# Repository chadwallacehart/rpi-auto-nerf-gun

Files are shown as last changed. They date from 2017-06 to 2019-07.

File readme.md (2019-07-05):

# Automatic Nerf Gun using a Rapsberry Pi

Make a software controlled Nerf Gun using a Raspberry Pi, a servo, and some 3D printed parts.

What you'll need:
* Nerf Revelle Rapid Red Blaster - <$12 on [Amazon](https://www.amazon.com/Nerf-Rebelle-Rapid-Red-Blaster/dp/B00INZO30M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)
* Raspberry Pi with one of the PCM GPIO pins available
* A 9g servo - like [these](https://www.amazon.com/s/ref=nb_sb_noss_1?url=search-alias%3Dtoys-and-games&field-keywords=9g+servo)
* Relay switch for the Raspberry Pi - I have an odd setup from an existing project so I don't discuss this
* Access to a 3D Printer - you can use an online service
* Some 18 to 22 guage wire
* Some aligator clips, appropriate jumper pins or a breakout board for the Pi

## Software

### Installation

```
git clone https://github.com/chadwallacehart/rpi-auto-nerf-gun.git
cd rpi-auto-nerf-gun
npm install
```

### Servo.js

Set the servo to a minimum value: `sudo node servo -40` - where the enumber is the minimum value

Set the servo to a min value and then max: `sudo node servo -40 270` - first parameter is min, second is max

Sweep the servo between whatever min and max value is in the code: `sudo node servo`

### gun.js

Shoot one bullet: `sudo node gun`

Shoot any number of darts: `sudo node gun 12` - fires 12 darts

## Hardware setup

### Servo Wiring
See Adafruit's [guide](https://learn.adafruit.com/adafruits-raspberry-pi-lesson-8-using-a-servo-motor/hardware) for how to set this up.

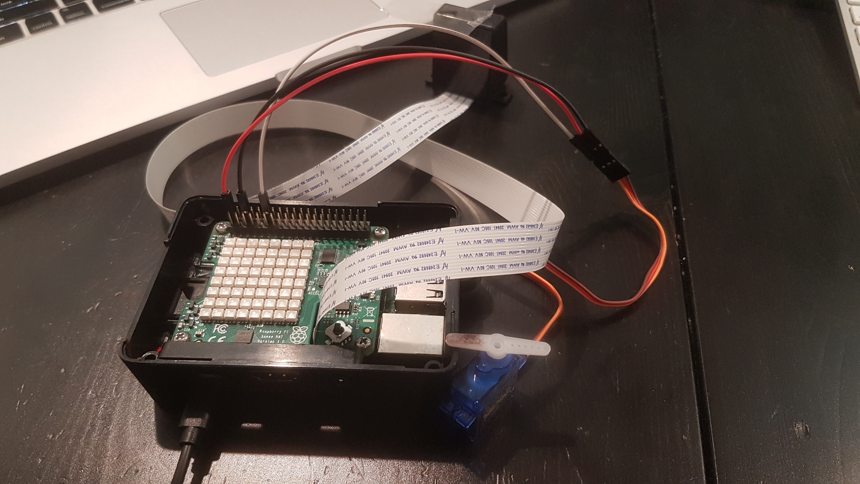
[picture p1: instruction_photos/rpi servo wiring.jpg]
Servo Setup Servo wiring


Use _servo.js_ to test.

_Note on powering_

Adafruit shows an external power supply, separate from the Raspberry Pi's. 
You shoud do this! I was able to do some tests powering directly from the Pi's 5V supply, but it was inconsistent and I wasn't being too safe. 
You can power the servo from your gun. Once you have your gun open (see below), use some aligator clips to power off of the nerf gun's batteries as shown here:

Nerf Gun wiring - servo power Powering the servo from the nerf gun

### Linear Actuator

See this [video](https://www.youtube.com/watch?v=qBHvMHJEG-M&t=1s) from Roger Rabbit of this in action.

You will need to 3d print this component and fit it inside the gun.

#### 3D printing parts

Grab the linear actuator 3D model in the repo [here](https://github.com/chadwallacehart/rpi-auto-nerf-gun/blob/master/CAD/servo%20linear%20actuator%20adjustment%203.stl).

I made a slight modification to [tscha70's](https://github.com/tscha70) [original design](https://github.com/tscha70/3DPrinterSTLFiles/tree/master/Proton%20Rev%202%20-%20Easter%20Edition) to change the size of the piston head square. 

The piston head is actually to square, so I ended up filing it down with a Dremel to look more like the angled profile of the original piston head. When I work on this again I will update the design so that this is not necessary.

#### Adjustment

You want to adjust the servo gear position so that it provides the maximum extension. 
To do this, take apart the linear relay piece so you just see the gear.

First find the minimum range. Run `sudo node servo n` with a range of values starting with 0.  
Keep decreasing _n_ until the decreasing the value makes no difference. For me this was `-40`. Mark this point.

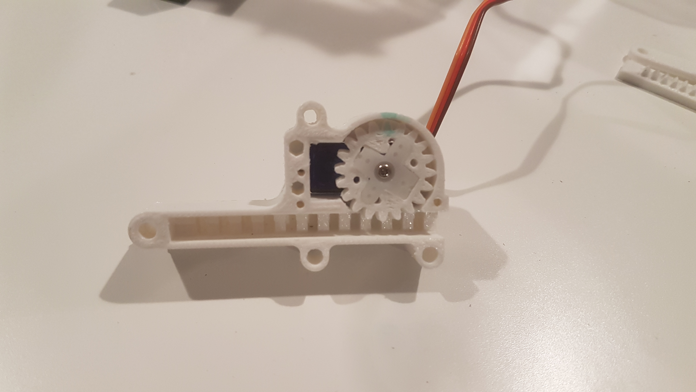
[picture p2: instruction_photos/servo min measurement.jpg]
Servo adjustment - minimum Find the servo minimium


Repeat this step to find the maximum range. Mine was `280`.

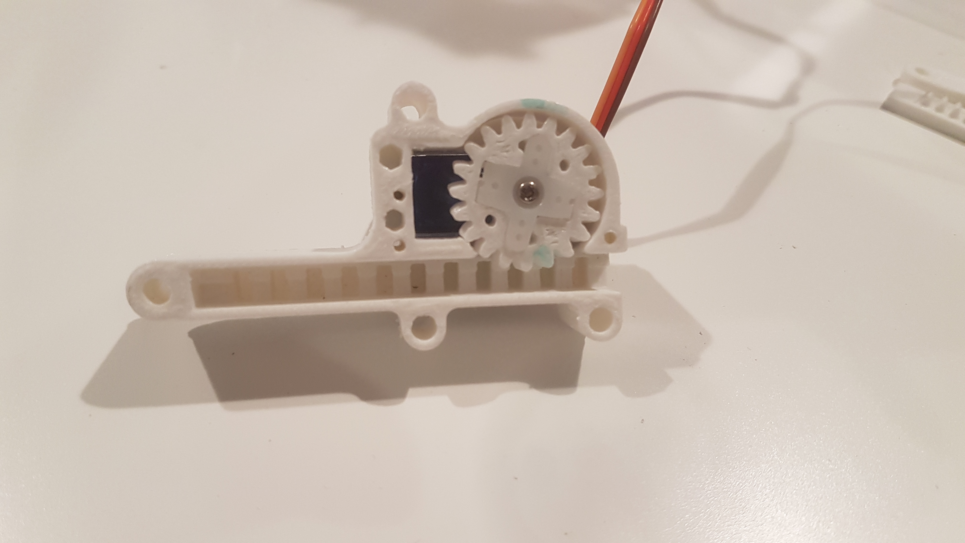
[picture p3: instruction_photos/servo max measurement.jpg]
Servo adjustment - maximum Find the servo maximum


After you find the maximum, make sure to reset the servo to its minimum point before re-assembling the linear servo.
When you are done you should have about a 38mm / 1.5 inch range.

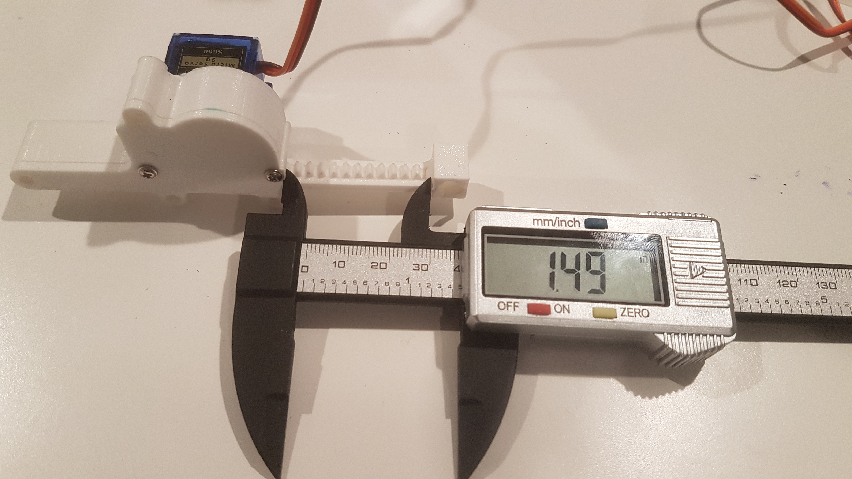
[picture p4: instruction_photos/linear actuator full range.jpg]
Adjusting to achieve the maximum linear servo range Test the servo to make sure you have the full range


Make sure to test the full range of motion many times before proceeding. 
Wiggle the actuator and simulate what will happen when you get a bit of friction and resitance to make sure the actuator gears stay in alignment.
The actuator will stop working if something gets misaligned inside.

I found that every time I opened the linear actuator and put it back together I had to adjust the min and max slightly.
In the end, you probably do not need the fill minimum and maximum range to fire a dart.

### Relay

See a good guide for setting this up [here](http://www.susa.net/wordpress/2012/06/raspberry-pi-relay-using-gpio/)

Below is a wiring diagram from that post, just note that instead of AC power we are just controlling the 2 6V motors that propel the nerf dart:

Relay Wiring Schematic for a relay via GPIO on the Raspberry Pi

### Wiring the gun

Now that the servo and relay are working, you need to permanently wire them to the gun.
Unfortunately I only had red, green, and black wire handy - it would have been helpful to have more colors.

I had to remove the motors and ran my wires down the original wire channel in the gun and out the trigger hole. See the _Assembled Photo_ below.

### Modifying the gun

If you have all the individual modules working above, the next step is fit the linear servo inside the gun.

You will need to trim some of the Rebelle gun plastic to make the linear servo fit inside. I used a Dremel tool to make this easy.

Maxing the actuator fit Trim some plastic from the gun to make the linear actuator fit

Place the linear actuator inside and trim only what you need.
When you have a decent fit on this half of the gun, then try running the linear actuator continuously to ensure it does not get caught on anything.
I cut a little too much, so I used hot glue (see the last picture below) to properly seat everything, being careful to make sure the actuator could fully extend.

The actuator is too wide to fit inside the gun and maintain alignment, so next you will need to cut a square hole on the opposite cover. 
Start by cutting a piece of tape that is exactly the size of the box part of the servo that sticks out of the linear actuator.
Put the opposite gun cover on.

The tape should stick in the right place. Use this as a template to cut a hole.

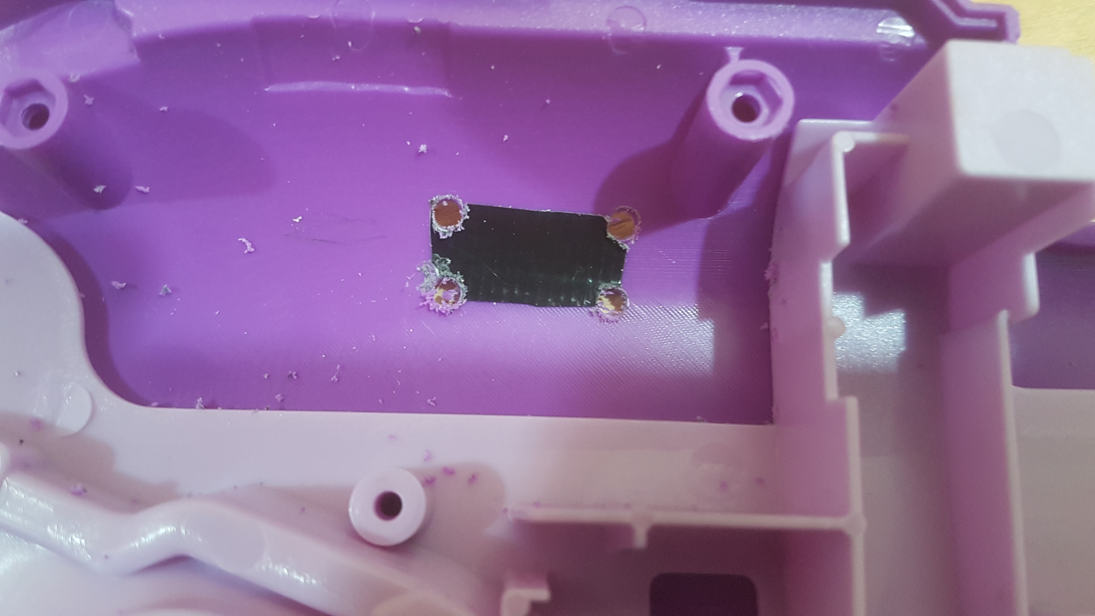
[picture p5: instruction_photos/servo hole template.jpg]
Cut a whole for the servo Use tape to make a template before cuttong a hole


Lastly you should be able to put the entire gun back together.
Make sure you keep testing the linear actuator alignment.

#### Assembled photo without cover

Nerf Gun wiring Nerf Gun Assembly

## Credits
* [Johnny-Five Project](http://johnny-five.io/) & [Nodebots](http://nodebots.io/)
* [Roger Rabbit](https://github.com/tscha70) for his outstanding [Linear Servo designs](https://github.com/tscha70/3DPrinterSTLFiles)

## Roadmap & To DO

- Make a video to better illustrate wiring & assembly
- Fix the linear servo piston head to mach the curved profile of the original piston head
- Investigate resizing the servo to better fit in the gun
- Use something other than j5's `servo.sweep` to see if it is possible to fire faster

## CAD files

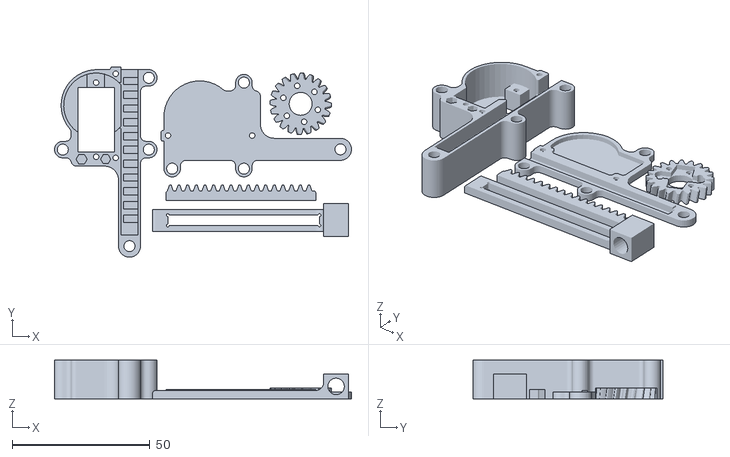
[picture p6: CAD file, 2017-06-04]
CAD/servo linear actuator adjustment 3.stl
107.7 x 69.0 x 14.0

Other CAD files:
CAD/servo linear actuator adjustment 3.skp

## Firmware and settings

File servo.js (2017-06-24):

const five = require("johnny-five");
const Raspi = require("raspi-io");
const board = new five.Board({
  io: new Raspi({includePins :['P1-12']})
});

let min = process.argv[2] || -80; //-80
let max = process.argv[3] || 270; 

board.on("ready", function() {
  let servo = new five.Servo({
	pin: "P1-12",
	range: [min,max],
	startAt: min
	});
  console.log("Instructions");
  console.log("Test min and max: sudo node servo [min] [max]");
  console.log("Sweep: sudo node servo");
  console.log();

  //sweep if no arguments
  if(!process.argv[2]){
  	console.log("sweeping from " + min + " to " + max);
	servo.sweep({interval:800});
	}
  //go to max if max argument provided
  else if(process.argv[3]) {
	console.log("Starting at " + min);
  	setTimeout(()=>
	  {
		console.log("Ending at " + max);
		servo.max();
		process.exit();

	  }, 500);
	}
  else{
	console.log("Starting at " + min);
	process.exit();
	}

});

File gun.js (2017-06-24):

const five = require("johnny-five");
const Raspi = require("raspi-io");
const board = new five.Board({
    io: new Raspi({includePins :['P1-12', 'GPIO12']})   //only init needed pins
});

let min = -40,
    max = 280;

let servo, gun;

let bullets = process.argv[2] || 1;

board.on("ready", function () {
    servo = new five.Servo({
        pin: "P1-12",
        range: [min, max],
        startAt: min
    });

    gun = new five.Pin('GPIO12');
    gun.low();  //initialize to low

    shoot2(bullets);

});


//function using sweep
function shoot2(count){

    let interval = 600;

    function stop(){
        console.log("turning off gun");
        gun.low();
        process.exit();
    }

    function fire(){
        servo.sweep({interval:interval});
        setTimeout(()=>{
            servo.stop();
            servo.min();
            stop();
        }, count*interval*2);
    }

    console.log("Turning on gun. Ready to fire " + count + " times");
    gun.high();
    setTimeout(() => {fire()}, 2500);

}

//function using min and max
//todo: debug - min never fires until the end
function shoot(shots){

    let counter = 1;

    function fire(){
        console.log("shot #" + counter);
        //console.time("fire");
        servo.stop();
        servo.max();

        setTimeout(()=>{
            console.log("I should be going to " + min + " now");
            servo.to(min);
            //console.timeEnd("fire");
            if (counter >= shots){
                stop();
            }
            else{
                counter++;
                fire();
            }
        }, 2000);
    }

    function stop(){
        console.log("turning off gun");
        gun.low();
        process.exit();
    }

    console.log("Turning on gun. Ready to fire " + shots + " times");
    gun.high();
    //give the gun some time to spin up
    setTimeout(() => {fire()}, 2500);
}

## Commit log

2017-06-04 expanding to include eveything
    renamed from rpiservotest. Adding all files related to nerf gun project
    [servo linear actuator adjustment 3.skp, servo linear actuator adjustment 3.stl]
2017-06-24 Add used pins to Raspi setup to prevent GPIO initializion conflicts in Johnny Five
    [gun.js, servo.js]
